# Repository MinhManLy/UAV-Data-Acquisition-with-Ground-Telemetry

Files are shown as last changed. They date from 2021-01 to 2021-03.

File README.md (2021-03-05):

# UAV Data Acquisition with Ground Telemetry
Arduino-based project using sensors and transceivers

Project team: Nicolas Rayner, Khaileb Freeman, Gus Pfitzner & Minh Man Ly

Project started on Friday 5th Jan 2021 and completed on Thursday 4th Feb 2021. The competed product is handed over to Flight One Academy.

Important note: 3D Enclosures - Autodesk Fusion 360 were done by Khaileb Freeman.

# Project description:
The project is to create sensor device for quadcopter drones (e.g Mavic Pro DJI drone) that acts just like some of the flight instruments used in crewed aircraft. This device collects data on temperature, pressure, altitude, and drone orientation and then transmits these real-time data to ground-based telemetry. Another part in the product of the project is the ground-based telemetry. Commands and communication can be made wirelessly between drones and ground station via transceiver modules of same RF band. Examples of the commands from ground station to drone sensors are resetting altitude to 0m and calibrating drone orientation before drone takes off.

Onboard sensors and ground-based telemetry are made on PCB circuit boards and enclosed in 3D printed housings. Onboard sensors and ground-based telemetry are designed to have successful communication from at least 1000m in distance and 100m in height. The 3D housings of the completed PCB circuit board for onboard sensors must fit to the quadcopter drone and the installation must be ensured not to violate thermodynamic operation of the drone and not to affect the IMU.
The project product – drone sensors and telemetry – will be tested and demonstrated in accordance with Drone Rules established by the Australian Civil Aviation Safety Authority. The RF band of the transceivers must meet the legal RF band use for ISM purposes established by Australian Government.
The project is sponsored by Flight One Academy - Archerfield, QLD, Australia.
 
# Components:
2 devices will be made in this project: the drone sensors and the telemetry on ground station. Components used in this project include:
+ Microcontroller: Arduino Nano
+ Sensors: IMU (MPU-6050) & Barometric sensor (BMP280)
+ Transmitter & Receiver: 433/868/915MHz Transceivers (nRF905)
+ Telemetry: LCD2004 display with I2C

# Libraries:
Below is the arduino libraries used in the project:

For ground-based telemetry:
+ <Wire.h>
+ <SPI.h>
+ <LiquidCrystal_I2C.h>
+ <nRF905.h> (from Zak Kemble)

For onboard drone sensor:
+ <nRF905.h> (from Zak Kemble)
+ <SPI.h>
+ <Adafruit_BMP280.h> 
+ <Wire.h>
+ "I2Cdev.h" (from Jeff Rowberg - MPU6050)
+ "MPU6050_6Axis_MotionApps20.h" (from Jeff Rowberg - MPU6050)

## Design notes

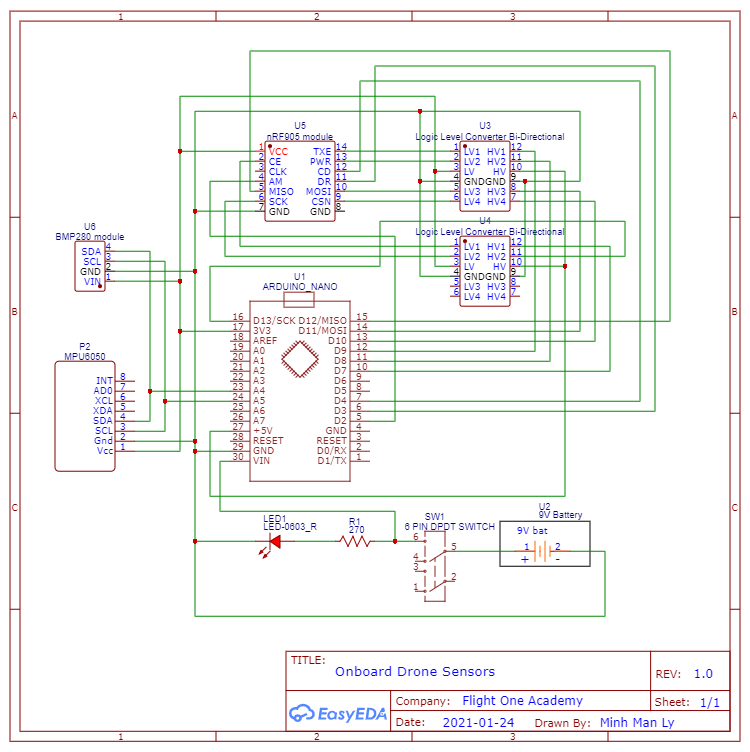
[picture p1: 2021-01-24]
Circuit diagrams/Onboard Drone Sensors.png

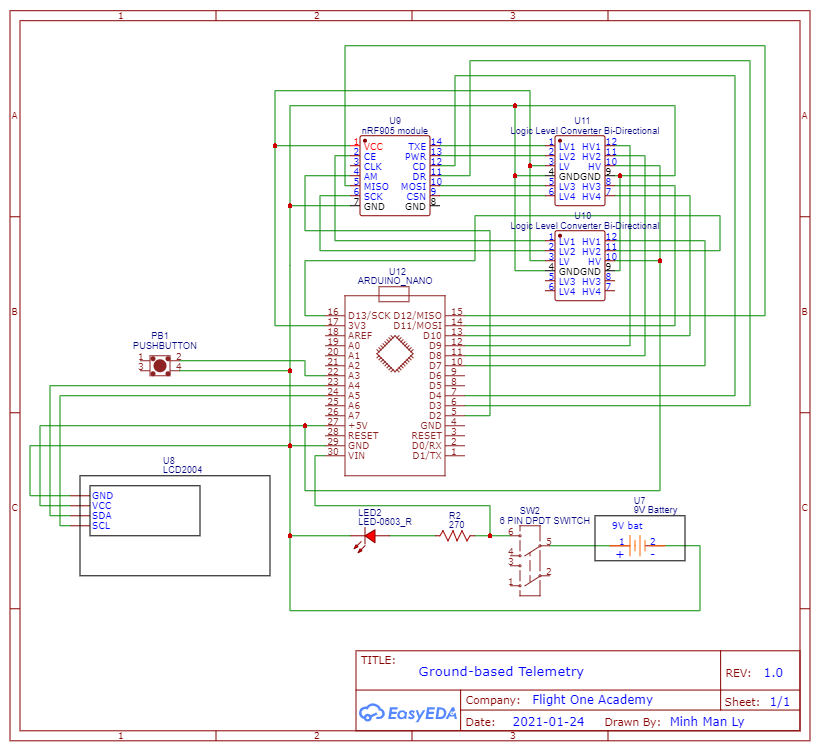
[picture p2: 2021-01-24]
Circuit diagrams/Ground-based Telemetry.png

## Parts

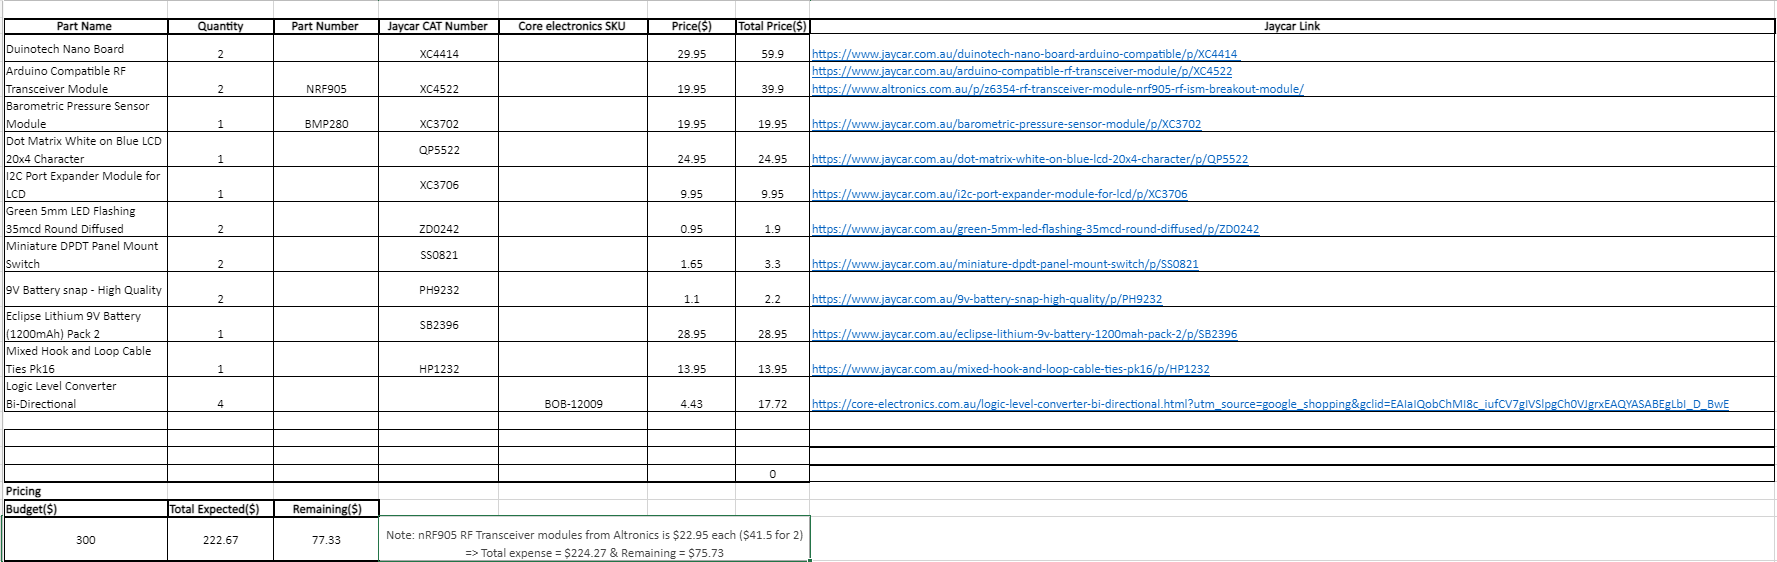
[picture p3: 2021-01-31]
Components/image.png

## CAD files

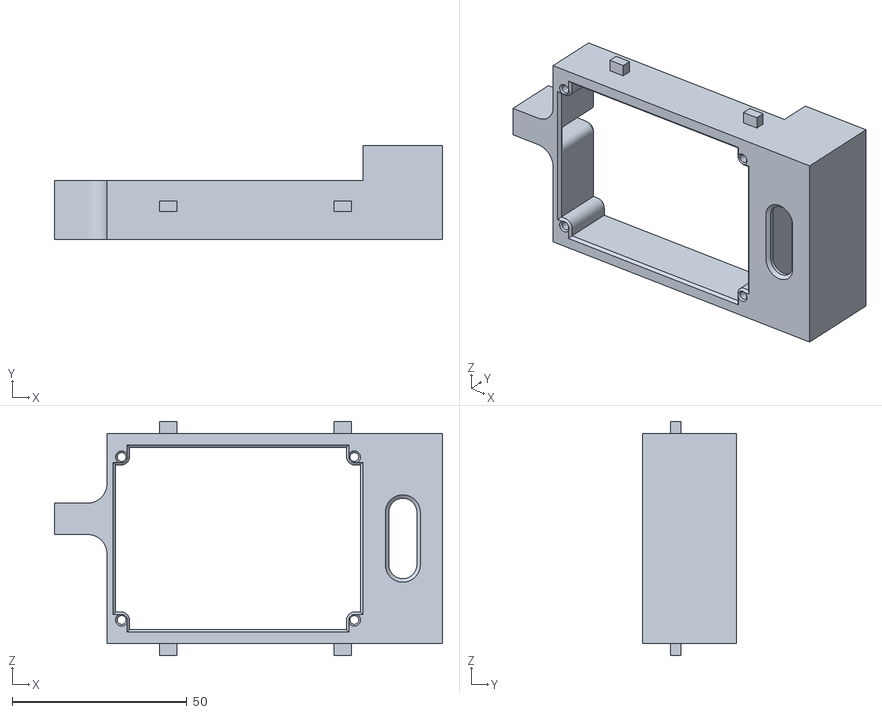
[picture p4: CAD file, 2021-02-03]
3D Enclosures - Autodesk Fusion 360/AAArduino holder v2000.stl
111.0 x 27.0 x 67.0

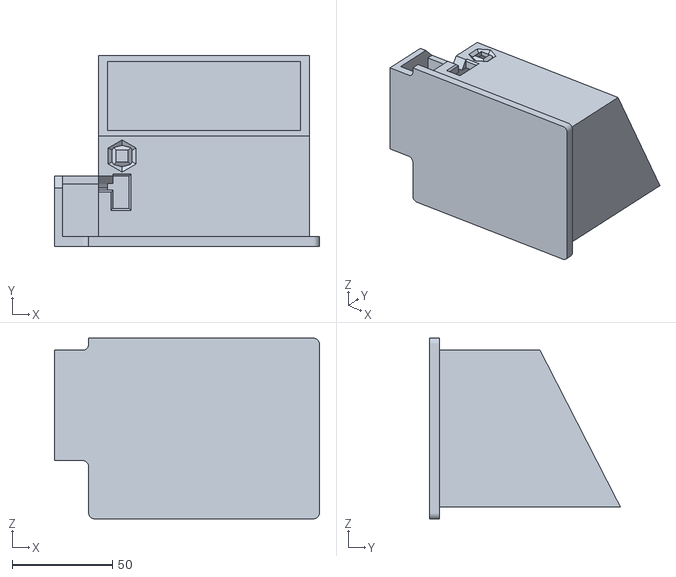
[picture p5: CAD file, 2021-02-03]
3D Enclosures - Autodesk Fusion 360/AAgroungcontrol.stl
132.0 x 95.0 x 90.0

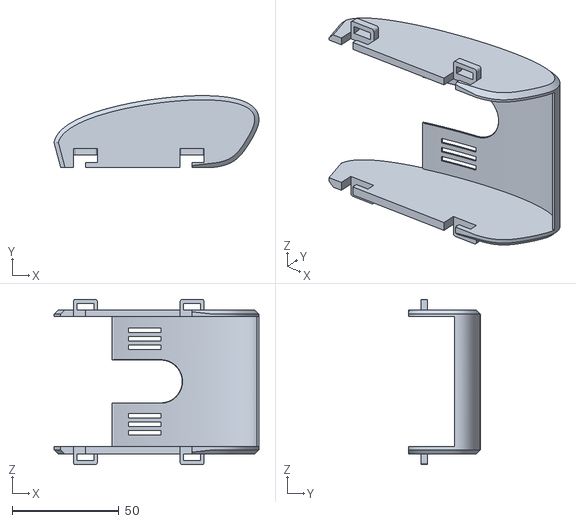
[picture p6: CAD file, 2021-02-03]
3D Enclosures - Autodesk Fusion 360/AADrone Cover.stl
96.0 x 33.6 x 77.5

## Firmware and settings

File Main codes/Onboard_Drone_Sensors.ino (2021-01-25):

/* ONBOARD DRONE SENSORS PROGRAM CODE
 * Project: UAV Real-time Data Acquisition with Wireless Telemetry
 * Author: Minh Man Ly
 * Co-authors: Nicolas Rayner, Khaileb Freeman & Gus Pfitzner
 * Reference: Zak Kemble & Jeff Rowberg
 * Sponsor: Flight One Academy - Archerfield, QLD, Australia
 * Circuit schematic: Available on the website below (Github)
 * Web link: https://github.com/MinhManLy/UAV-Data-Acquisition-with-Ground-Telemetry
 * This program code is not the low power consumption version. Yet, the code is still 
in accordance with legal RF band for ISM purpose in Australia - 433MHz & less than 25mW power output 
 */

// =============================================================================================== //
// ===                                        LIBRARIES                                        === //
// =============================================================================================== //

#include <nRF905.h>
#include <SPI.h>
#include <Adafruit_BMP280.h>
#include <Wire.h>
#include "I2Cdev.h"
#include "MPU6050_6Axis_MotionApps20.h"
//#include "MPU6050.h"              // Not necessary if using MotionApps include file

#if I2CDEV_IMPLEMENTATION == I2CDEV_ARDUINO_WIRE  // Arduino Wire library is required if I2Cdev I2CDEV_ARDUINO_WIRE implementation is used in I2Cdev.h
    #include "Wire.h"
#endif

// =============================================================================================== //
// ===                              PINS & VARIABLES DECLARATION                               === //
// =============================================================================================== //

#define RXADDR 0xE7E7E7E7           // Address of this device (drone sensors)
#define TXADDR 0xE7E7E7E7           // Address of device to send to (ground station)
#define NODE_ID        78           // No actual use

#define TIMEOUT 200                 // Define refresh rate/transmission rate for drone sensor receive (recommmend: 100ms -> 500ms ping timeout)

#define PACKET_NONE		0             // No data detected
#define PACKET_OK		1               // Data detected
#define PACKET_INVALID	2           // Bad/invalid data detected

#define PAYLOAD_SIZE	NRF905_MAX_PAYLOAD  // Max size of data packet (buffer) = 32

#define initialiseLED A0            // LED to signal the completion of setup (not use)

float pressure, temp, altitude;
float ground_pressure, total_pressure;

nRF905 transceiver = nRF905();      // Define transceiver used - nRF905
Adafruit_BMP280 bmp; // I2C         // Define barometric sensor used - BMP280

MPU6050 mpu;                        // Class default I2C address is 0x68
//MPU6050 mpu(0x69);                // <-- use for AD0 high

#define OUTPUT_READABLE_YAWPITCHROLL

//#define INTERRUPT_PIN 2           // Use pin 2 on Arduino Uno & most boards //NOT USED FOR MPU6050 as nRF905 is using it

float pitch, roll, yaw;             // Declare int/float orientation vars for 1m/1.00m resolution

static volatile uint8_t packetStatus;

// ===                                MPU CONTROL/STATUS VARS                                  === //
bool dmpReady = false;              // Set true if DMP init was successful
uint8_t mpuIntStatus;               // Holds actual interrupt status byte from MPU
uint8_t devStatus;                  // Return status after each device operation (0 = success, !0 = error)
uint16_t packetSize;                // Expected DMP packet size (default is 42 bytes)
uint16_t fifoCount;                 // Count of all bytes currently in FIFO
uint8_t fifoBuffer[64];             // FIFO storage buffer

// ===                                ORIENTATION/MOTION VARS                                  === //
Quaternion q;                       // [w, x, y, z]         quaternion container
VectorInt16 aa;                     // [x, y, z]            accel sensor measurements
VectorInt16 aaReal;                 // [x, y, z]            gravity-free accel sensor measurements
VectorInt16 aaWorld;                // [x, y, z]            world-frame accel sensor measurements
VectorFloat gravity;                // [x, y, z]            gravity vector
float euler[3];                     // [psi, theta, phi]    Euler angle container
float ypr[3];                       // [yaw, pitch, roll]   yaw/pitch/roll container and gravity vector

// =============================================================================================== //
// ===                                    INTERRUPT SETUPS                                     === //
// =============================================================================================== //

// NOT USED IN THIS PROGRAM
//volatile bool mpuInterrupt = false;     // Indicates whether MPU interrupt pin has gone high
//void dmpDataReady() {
    //mpuInterrupt = true;
//}

// Don't modify these 2 functions. They just pass the DR/AM interrupt to the correct nRF905 instance.
void nRF905_int_dr(){transceiver.interrupt_dr();}
void nRF905_int_am(){transceiver.interrupt_am();}

// =============================================================================================== //
// ===                                  FUNCTIONS DEFINITION                                   === //
// =============================================================================================== //

// Event function for RX complete
void nRF905_onRxComplete(nRF905* device)
{
	packetStatus = PACKET_OK;
	transceiver.standby();
}

// Event function for RX invalid
void nRF905_onRxInvalid(nRF905* device)
{
	packetStatus = PACKET_INVALID;
	transceiver.standby();
}

// =============================================================================================== //
// ===                                    INITIAL SETUPS                                       === //
// =============================================================================================== //

void setup() {
  #if I2CDEV_IMPLEMENTATION == I2CDEV_ARDUINO_WIRE            // Join I2C bus (I2Cdev library doesn't do this automatically)
    Wire.begin();
    Wire.setClock(400000);                                    // 400kHz I2C clock. Comment this line if having compilation difficulties
  #elif I2CDEV_IMPLEMENTATION == I2CDEV_BUILTIN_FASTWIRE
    Fastwire::setup(400, true);
  #endif
  
  pinMode(initialiseLED, OUTPUT);
  digitalWrite(initialiseLED, LOW);
  
	Serial.begin(115200);
  while (!Serial);                                            // Wait for Leonardo enumeration, others continue immediately
  
  //Serial.println(F("Initializing I2C devices..."));         // For troubleshooting
  mpu.initialize();                                           // Initialize device
  //pinMode(INTERRUPT_PIN, INPUT); //NOT USED FOR MPU6050 as nRF905 is using it
  Serial.println(F("Testing device connections..."));         // Verify connection
  Serial.println(mpu.testConnection() ? F("MPU6050 connection successful") : F("MPU6050 connection failed"));

  // wait for ready
  //Serial.println(F("\nSend any character to begin DMP programming and demo: "));
  while (Serial.available() && Serial.read());                // Empty buffer
  //while (!Serial.available());                              // Wait for data
  //delay(1000);
  while (Serial.available() && Serial.read());                // Empty buffer again
  
  Serial.println(F("Initializing DMP..."));
  devStatus = mpu.dmpInitialize();                            // Load and configure the DMP
  
  // Supply your own gyro offsets here, scaled for min sensitivity
  mpu.setXGyroOffset(220);
  mpu.setYGyroOffset(76);
  mpu.setZGyroOffset(-85);
  mpu.setZAccelOffset(1788);                                  // 1688 factory default for Jeff Rowberg's test chip

  if (devStatus == 0) {                                       // Make sure it worked (returns 0 if so)
    mpu.CalibrateAccel(6);                                    // Calibration Time: generate offsets and calibrate our MPU6050
    mpu.CalibrateGyro(6);
    mpu.PrintActiveOffsets();
    
    //Serial.println(F("Enabling DMP..."));
    mpu.setDMPEnabled(true);                                  // Turn on the DMP, now that it's ready

    // enable Arduino interrupt detection
    //Serial.print(F("Enabling interrupt detection (Arduino external interrupt "));
    //Serial.print(digitalPinToInterrupt(INTERRUPT_PIN));
    //Serial.println(F(")..."));
    //attachInterrupt(digitalPinToInterrupt(INTERRUPT_PIN), dmpDataReady, RISING); //INTERRUPT NOT USED FOR MPU6050 as nRF905 is using it
    mpuIntStatus = mpu.getIntStatus();

    // set our DMP Ready flag so the main loop() function knows it's okay to use it
    //Serial.println(F("DMP ready! Waiting for first interrupt..."));
    dmpReady = true;

    // get expected DMP packet size for later comparison
    packetSize = mpu.dmpGetFIFOPacketSize();
  } 
  else {
    // ERROR!
    // 1 = initial memory load failed
    // 2 = DMP configuration updates failed
    // (if it's going to break, usually the code will be 1)
    //Serial.print(F("DMP Initialization failed (code "));
    //Serial.print(devStatus);
    //Serial.println(F(")"));
  }
  
  /* For debugging Barometric sensor
	if (!bmp.begin()) {
    Serial.println(F("Could not find a valid BMP280 sensor, check wiring!"));
    while (1);
  }
  */
	
	// Standby off
	//pinMode(7, OUTPUT); 
	//digitalWrite(7, HIGH);
	
	SPI.begin();                                                  // This must be called first
  
	transceiver.begin(                                            // All wires, maximum functionality for nRF905
		SPI,      // SPI bus to use (SPI, SPI1, SPI2 etc)
		10000000, // SPI Clock speed (10MHz)
		10, // SPI SS
		7,  // CE (standby)
		9,  // TRX (RX/TX mode)
		8,  // PWR (power down)
		4,  // CD (collision avoid)
		3,  // DR (data ready)
		2,  // AM (address match)
		nRF905_int_dr,  // Interrupt function for DR
		nRF905_int_am   // Interrupt function for AM
	);

/*
	// Minimal wires (polling)
	// Up to 5 wires can be disconnected, however this will reduce functionality and will put the library into polling mode instead of interrupt mode
	// In polling mode the .poll() method must be called as often as possible. If .poll() is not called often enough then events may be missed. (Search for .poll() in the loop() function below)
	transceiver.begin(
		SPI,
		10000000,
		6,
		NRF905_PIN_UNUSED, // CE (standby) pin must be connected to VCC (3.3V) - Will always be in RX or TX mode
		9, // TRX (RX/TX mode)
		NRF905_PIN_UNUSED, // PWR pin must be connected to VCC (3.3V) - Will always be powered up
		NRF905_PIN_UNUSED, // Without the CD pin collision avoidance will be disabled
		NRF905_PIN_UNUSED, // Without the DR pin the library will run in polling mode and poll the status register over SPI. This also means the nRF905 can not wake the MCU up from sleep mode
		NRF905_PIN_UNUSED, // Without the AM pin the library the library must poll the status register over SPI.
		NULL, // No interrupt function
		NULL // No interrupt function
	);
*/

/*
	// Minimal wires (interrupt)
	// Up to 4 wires can be disconnected, however this will reduce functionality.
	// onAddrMatch and onRxInvalid events will not work with this configuration as they rely on the AM interrupt.
	transceiver.begin(
		SPI,
		10000000,
		6,
		NRF905_PIN_UNUSED, // CE (standby) pin must be connected to VCC (3.3V) - Will always be in RX or TX mode
		9, // TRX (RX/TX mode)
		NRF905_PIN_UNUSED, // PWR pin must be connected to VCC (3.3V) - Will always be powered up
		NRF905_PIN_UNUSED, // Without the CD pin collision avoidance will be disabled
		3, // DR (data ready)
		NRF905_PIN_UNUSED, // Without the AM pin the library must poll the status register over SPI.
		nRF905_int_dr,
		NULL // No interrupt function
	);
*/

	transceiver.events(                                   // Register event functions
		nRF905_onRxComplete,
		nRF905_onRxInvalid,
		NULL,
		NULL
	);

	transceiver.setListenAddress(TXADDR);                 // Set address of this device
 
  // Set channel and band for legal ISM use in Australia
  // NOTE: we can either use 433 or 915MHz as 433MHz output power is 
//10dBm (10mW). Prefer to nRF905_config -> NRF905_PWR = NRF905_PWR_10 (10dBm = 10mW)
  transceiver.setBand(NRF905_BAND_433);
  transceiver.setChannel(10);

  bmp.begin();                                          // Set up the Barometric sensor
  
  // Default settings from datasheet
  bmp.setSampling(Adafruit_BMP280::MODE_NORMAL,         // Operating Mode.
                  Adafruit_BMP280::SAMPLING_X2,         // Temp. oversampling
                  Adafruit_BMP280::SAMPLING_X16,        // Pressure oversampling
                  Adafruit_BMP280::FILTER_X16,          // Filtering.
                  Adafruit_BMP280::STANDBY_MS_500);     // Standby time.
                  
  // Getting average temperature and pressure for ground station
  // Altitude at ground station is approximately 0 meter
  total_pressure = 0;
  for (int i = 1; i <= 50; i++) {   //50 measurements
    pressure = bmp.readPressure();
    total_pressure += pressure;
    //Serial.print("    ");
    //Serial.println(total_pressure);
    delay(50);                                          // Total delay time = 50 * 50 = 2.5 secs
  }
  ground_pressure = total_pressure/50.;
  
	Serial.println(F("Onboard drone sensor - setup completed"));
  //digitalWrite(initialiseLED, HIGH);
}

// =============================================================================================== //
// ===                                    MAIN PROGRAM LOOP                                    === //
// =============================================================================================== //

void loop()
{
	static uint8_t counter;                                   // Not use
  
  temp = bmp.readTemperature();                             // Store float value of temperature (*C) in 'temp'
  pressure = bmp.readPressure();                            // Store float value of pressure (Pa) in 'pressure'
  altitude = bmp.readAltitude(ground_pressure/100.);        // Store float value of altitude (m) in 'altitude'. Altitude is calculated by divided the average ground pressure taken at the end of set ups by 100 (100 is to convert Pa -> hPa)
  int temp_int = temp*100;                                  // Move decimal point 2 places to the right (e.g temp = 25.23*C -> temp_int = 2523*C) => This is the number later be sent from this device to ground statino telemetry
  long int pressure_int = pressure;                         // Float-type pressure (Pa) is converted to long int-type pressure (Pa) (e.g pressure = 101748.21Pa - > pressure_int = 101748Pa)
  int altitude_int = altitude*100;                          // Move decimal point 2 places to the right (e.g altitude = 3.25m -> altitude_int = 325m) => This is the number later be sent from this device to ground statino telemetry

  Orientation_Reader();                                     // Read data from MPU6050 IMU

  int yaw_int = yaw*100;                                    // Move decimal point 2 places to the right (e.g yaw = 12.25 -> yaw_int = 1225) => This is the number later be sent from this device to ground statino telemetry
  int pitch_int = pitch*100;                                // Move decimal point 2 places to the right (e.g pitch = 12.25 -> pitch_int = 1225) => This is the number later be sent from this device to ground statino telemetry
  int roll_int = roll*100;                                  // Move decimal point 2 places to the right (e.g roll = 12.25 -> roll_int = 1225) => This is the number later be sent from this device to ground statino telemetry
  
	int32_t buffer[PAYLOAD_SIZE];                             // Make data 
	//memset(buffer, counter, PAYLOAD_SIZE);
	//counter++;
  packetStatus = PACKET_NONE;

  // BMP280 data
  buffer[1] = temp_int>>8;
  buffer[2] = temp_int;
  buffer[3] = pressure_int>>8;
  buffer[4] = pressure_int;
  buffer[5] = altitude_int>>8;
  buffer[6] = altitude_int;
  // MPU6050 data
  buffer[0] = pitch_int>>0;
  buffer[7] = roll_int>>0;

  // Need more testings
  //buffer[8] = yaw_int>>0;
  //buffer[9] = pitch_int>>0;
  //buffer[10] = pitch_int;
  //buffer[11] = roll_int>>0;
  //buffer[12] = roll_int;

  Serial.print(F("Barometric sensor values: "));            // Show data
  Serial.print(temp_int);
  Serial.print(F(" "));
  Serial.print(pressure_int);
  Serial.print(F(" "));
  Serial.println(altitude_int);
  Serial.print(F("IMU values: "));
  Serial.print("yaw not work");
  Serial.print(F(" "));
  Serial.print(buffer[0]);
  Serial.print(F(" "));
  Serial.println(buffer[7]);
  //packetStatus = PACKET_NONE;
  
//                                   Transceiver in Transmit mode                                  //
	Serial.println(F("Sending data... "));
	// Write reply data and destination address to radio IC
	transceiver.write(TXADDR, buffer, sizeof(buffer));
  
  //packetStatus = PACKET_NONE;
  uint32_t startTime = millis();

//                                    Transceiver in Receive mode                                  //
	while(!transceiver.TX(NRF905_NEXTMODE_RX, true));         // Send the data (send fails if other transmissions are going on, keep trying until success) and enter RX mode on completion
	
	Serial.println(F("Waiting for reply..."));                // Receive reply (replyBuffer) from ground station

  uint8_t success;

  uint32_t sendStartTime = millis();                        // Wait for reply with timeout
  while(1)  {
    //transceiver.poll();                                   // Uncomment this line if the library is running in polling mode

    success = packetStatus;
    if(success != PACKET_NONE)
      break;
    else if(millis() - sendStartTime > TIMEOUT)
      break;
  }

  if(success == PACKET_NONE)
  {
    Serial.println(F("Receiving ground data timed out > 200ms"));
    //timeouts++;
  }
  else if(success == PACKET_INVALID)
  {
    Serial.println(F("Invalid packet!"));
    //invalids++;
  }
  else
  {
    uint16_t totalTime = millis() - startTime;
    //replies++;
  
    // If success send ping time over serial
    Serial.print(F("Ping time: "));
    Serial.print(totalTime);
    Serial.println(F("ms"));
    
		// Get the reply data // NOT WORK YET
		uint8_t replyBuffer[PAYLOAD_SIZE];
		transceiver.read(replyBuffer, sizeof(replyBuffer));
    
		// Show received data
    Serial.print(replyBuffer[0], DEC);
    Serial.print(F(" "));
    Serial.print(replyBuffer[1], DEC);
    Serial.print(F(" "));
    Serial.print(replyBuffer[2], DEC);
    Serial.println();
    Serial.print(replyBuffer[3], DEC);
    Serial.println();

    // Reset ground altitude (1 1 0 0)
    if (replyBuffer[0] == 1 && replyBuffer[1] == 1)  {
      Serial.println("RESET GROUND ALTITUDE");
      Serial.print("GROUND PRESSURE RESET TO ");
      Reset_ground_pressure();
      Serial.println(ground_pressure);
    }
    // Reset pitch and roll (0 0 1 1)
    if (replyBuffer[2] == 1 && replyBuffer[3] == 1) {
      Serial.println("RESET MPU6050");
      Reset_MPU_DMP();
      Serial.print("Inertial Measurement Unit has been reset");
    }
  }
  Serial.flush();
    
  // Delay is for debugging
	//delay(500);
}

// =============================================================================================== //
// ===                                  FUNCTIONS DEFINITION                                   === //
// =============================================================================================== //

void Orientation_Reader() {
    // if programming failed, don't try to do anything
    if (!dmpReady) return;                                  // Read a packet from FIFO
    if (mpu.dmpGetCurrentFIFOPacket(fifoBuffer)) {          // Get the Latest packet 
            mpu.dmpGetQuaternion(&q, fifoBuffer);           // Display Euler angles in degrees
            mpu.dmpGetGravity(&gravity, &q);
            mpu.dmpGetYawPitchRoll(ypr, &q, &gravity);
            Serial.print("Yaw = ");
            yaw = ypr[0] * 180/M_PI;
            Serial.print(yaw);
            Serial.print(" | Pitch = ");
            pitch = ypr[1] * 180/M_PI;
            Serial.print(pitch);
            Serial.print(" | Roll = ");
            roll = ypr[2] * 180/M_PI;
            Serial.println(roll);
    }
}

void Reset_ground_pressure() {
  // Getting average temperature and pressure for ground station
  // Altitude at ground station is approximately 0 meter
  float total_pressure = 0;
  float temporary_pressure;
  for (int j = 1; j <= 50; j++) {             //50 measurements
    temporary_pressure = bmp.readPressure();
    total_pressure += temporary_pressure;
    delay(50);
  }
  ground_pressure = total_pressure/50.;
}
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

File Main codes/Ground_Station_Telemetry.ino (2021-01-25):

/* GROUND-BASED TELEMETRY PROGRAM CODE
 * Project: UAV Real-time Data Acquisition with Wireless Telemetry
 * Author: Minh Man Ly
 * Co-authors: Nicolas Rayner, Khaileb Freeman & Gus Pfitzner
 * Reference: Zak Kemble & Jeff Rowberg
 * Sponsor: Flight One Academy - Archerfield, QLD, Australia
 * Circuit schematic: Available on the website below (Github)
 * Web link: https://github.com/MinhManLy/UAV-Data-Acquisition-with-Ground-Telemetry
 * This program code is not the low power consumption version. Yet, the code is still 
in accordance with legal RF band for ISM purpose in Australia - 433MHz & less than 25mW power output 
 */

// =============================================================================================== //
// ===                                        LIBRARIES                                        === //
// =============================================================================================== //

#include <Wire.h>
#include <SPI.h>
#include <LiquidCrystal_I2C.h>
#include <nRF905.h>

// =============================================================================================== //
// ===                              PINS & VARIABLES DECLARATION                               === //
// =============================================================================================== //

#define RXADDR 0xE7E7E7E7   // Address of this device (ground station)
#define TXADDR 0xE7E7E7E7   // Address of device to send to (drone sensors)

#define PACKET_NONE		0     // No data detected
#define PACKET_OK		1       // Data detected
#define PACKET_INVALID	2   // Bad/invalid data detected

#define PAYLOAD_SIZE	NRF905_MAX_PAYLOAD  // Max size of data packet (buffer) = 32

#define button1 A3          // Pushbutton to change display mode, reset altitude & re-calibrate pitch/roll (connect to Arduino A3 and GND)
int button1_current;        // Current pushbutton state to change display mode
int button1_previous = 0;   // Previous pushbutton state to change display mode
int lcd_state;              // State of LCD display of different modes (TPA reader or Orientation mode)

int count;                  // Count the duration of pushbutton being pushed to change display modes - Can use millis() function instead of counter
//long time_count;          // (For testing) The last time the output pin was toggled
//long debounce = 200;      // (For testing) The debounce time, increase if the output flickers

nRF905 transceiver = nRF905();            // Define transceiver used - nRF905
LiquidCrystal_I2C lcd(0x27,20,4);         // Define lcd display used - LCD2004_I2C

static volatile uint8_t packetStatus;     // Status of data packet
uint8_t replyBuffer[PAYLOAD_SIZE];        // Reply data buffer from this device (ground station) to receiver device (drone sensors) of same address\

// =============================================================================================== //
// ===                                    INTERRUPT SETUPS                                     === //
// =============================================================================================== //

// Don't modify these 2 functions. They just pass the DR/AM interrupt to the correct nRF905 instance.
void nRF905_int_dr(){transceiver.interrupt_dr();}   // Receive and transmit ready interrupt
void nRF905_int_am(){transceiver.interrupt_am();}   // Address matched interrupt

// =============================================================================================== //
// ===                                  FUNCTIONS DEFINITION                                   === //
// =============================================================================================== //

// Event function for RX complete
void nRF905_onRxComplete(nRF905* device)  {
	packetStatus = PACKET_OK;
	transceiver.standby();
}

// Event function for RX invalid
void nRF905_onRxInvalid(nRF905* device) {
	packetStatus = PACKET_INVALID;
	transceiver.standby();
}

// Make buffer for data
int32_t buffer[PAYLOAD_SIZE];     // Data buffer from other device (drone sensors) sent to this device (ground station)

// =============================================================================================== //
// ===                                     INITIAL SETUPS                                      === //
// =============================================================================================== //

void setup()  {
	Serial.begin(115200);           // Set up serial monitor for troubleshooting

  lcd.init();                     // Initialise LCD2004_I2C
  lcd.backlight();                // Turn on backlight for LCD2004_I2C (consume more current)
  //lcd.noBacklight;              // Turn off backlight
  lcd.setCursor(0,1);             // Display project team
  lcd.print("Designed by");
  lcd.setCursor(6,2);
  lcd.print("Octaltech Team");    // Madeup name of the project team (no trademark)
  delay(3000);                    // Delay is unecessary but is here to wait for drone sensor to finish initialisation
  
  pinMode(button1, INPUT_PULLUP); // Set up push button for changing mode
  
	//Serial.println(F("Server starting..."));    // For troubleshooting
  
  // This must be called first
	SPI.begin();                    // Set up SPI

	transceiver.begin(
		SPI,      // SPI bus to use (SPI, SPI1, SPI2 etc)
		10000000, // SPI Clock speed (10MHz)
		10, // SPI SS
		7,  // CE (standby)
		9,  // TRX (RX/TX mode)
		8,  // PWR (power down)
		4,  // CD (collision avoid)
		3,  // DR (data ready)
		2,  // AM (address match)
		nRF905_int_dr,  // Interrupt function for DR
		nRF905_int_am   // Interrupt function for AM
	);
	
	transceiver.events(                       // Register event functions
		nRF905_onRxComplete,
		nRF905_onRxInvalid,
		NULL,
		NULL
	);
	
	transceiver.setListenAddress(RXADDR);     // Set address of this device

  // Set channel and band for legal ISM use in Australia
  // NOTE: we can either use 433 or 915MHz as 433MHz output power is 
//10dBm (10mW) (legal for ISM use in Australia). Prefer to nRF905_config -> NRF905_PWR = NRF905_PWR_10 (10dBm = 10mW)
  transceiver.setBand(NRF905_BAND_433);
  transceiver.setChannel(10);

	transceiver.RX();         // Put into receive mode

  lcd_state = 0;            // Declare first display (TPA reader) that the lcd screen shows
  button1_previous = 0;     // Declare previous button state = 0 to toggle display when pushbutton is pressed

	//Serial.println(F("Server started"));    // For troubleshooting
  lcd.clear();
  lcd.setCursor(2,1);
  lcd.print("Waiting for data");
  lcd.setCursor(9,2);
  lcd.print("...");
  delay(1000);              // Delay is unecessary but is here to wait for data from drone sensor
}
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

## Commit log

2021-01-24 Create Ground-based telemetry circuit
2021-01-24 Create Circuit diagrams
